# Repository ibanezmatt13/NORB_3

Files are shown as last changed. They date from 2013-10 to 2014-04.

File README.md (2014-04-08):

WARNING - There is a slight design issue with the schematic for the PCB which I had to bodge to get the micro SD working. The VSS pins of the connector should be connected to a GND point on the board, which for some reason it isn't. So, I had to solder a wire going from the connector to a ground point on the board; not pretty but it works.

There are two scripts here, one for delay-driven RTTY, and one for interrupt-driven RTTY. The delay-driven code has been flown and proved to work perfectly; the interrupt-driven code works fine on the ground but has not had an approval flight just yet.

NORB 3
======
NORB 3 is the third generation in the NORB AVR-based HAB tracking PCB series. 

Main Components:
================

NTX2 434MHz Radio Transmitter

Ublox MAX 7 GPS Module

Amtel ATMEGA328P-AU Microcontroller

SHT11 Temperature/Humidity Sensor

TMP102 I2C Temperature Sensor

Micro SD socket

TPS61201 Step-up Boost Regulator

Taoglas GPS Antenna

Info
====

More information including the development, current status and pictures of the tracker can be found at NORB's website:

                                                  http://www.norb.co.uk

What NORB does...
=================

The current software that runs the NORB board does several things:

1.  It uses a special routine to search repeatedly for certain characters over a serial connection to the Ublox GPS         module. Once it picks up the correct beginning of what could be a valid NMEA sentence, it checks for the letter G to     to see if it is the correct sentence. If it is, it passes the sentence as a string to a parse_NMEA function.

2.  The parse_NMEA function is designed to carefully assess whether the sentence contains any anomalies in certain          fields. This could be a lost character during transfer or the sentence may not actually reflect a full GPS lock.        Should this be the case, the parsing is discontinued and the search for another sentence restarts. If it does get       through however, a few tasks are performed...

3.  The time is checked to assess what format it is in and to assess if it is a valid time value. Then the                  Latitude/longitude is converted into decimal degrees for uploading to the spacenear.us server after decoding. 

4.  After the sentence has been stripped down and individual fields of data have been analysed, the program will request     information from the SHT11 temperature and humidity sensor where upon it will parse the data into a suitable format.     The voltage across the battery is also analysed by scaling the analogue value on the correct analogue pin to a value     within the range 0v to 3.3v.

5.  Next, two strings are constructed: a log_datastring and a send_datastring. The log_datastring contains absolutely       all data including voltage and humidity, which will be logged to the SD card. The send_datastring contains only the     bare minimum of required data for basic telemetry, but I couldn't resist adding temperature in there too. I have        done this to further reduce the probability of a decoding error on the ground. ie, more data coming down = more         chance of a bad sentence.

6.  Then, we log the log_datastring to the SD card, and send the send_datastring down over the radio link by splitting      it up into binary digits to toggle the transmit pin on our transmitter. And there you have it! :D

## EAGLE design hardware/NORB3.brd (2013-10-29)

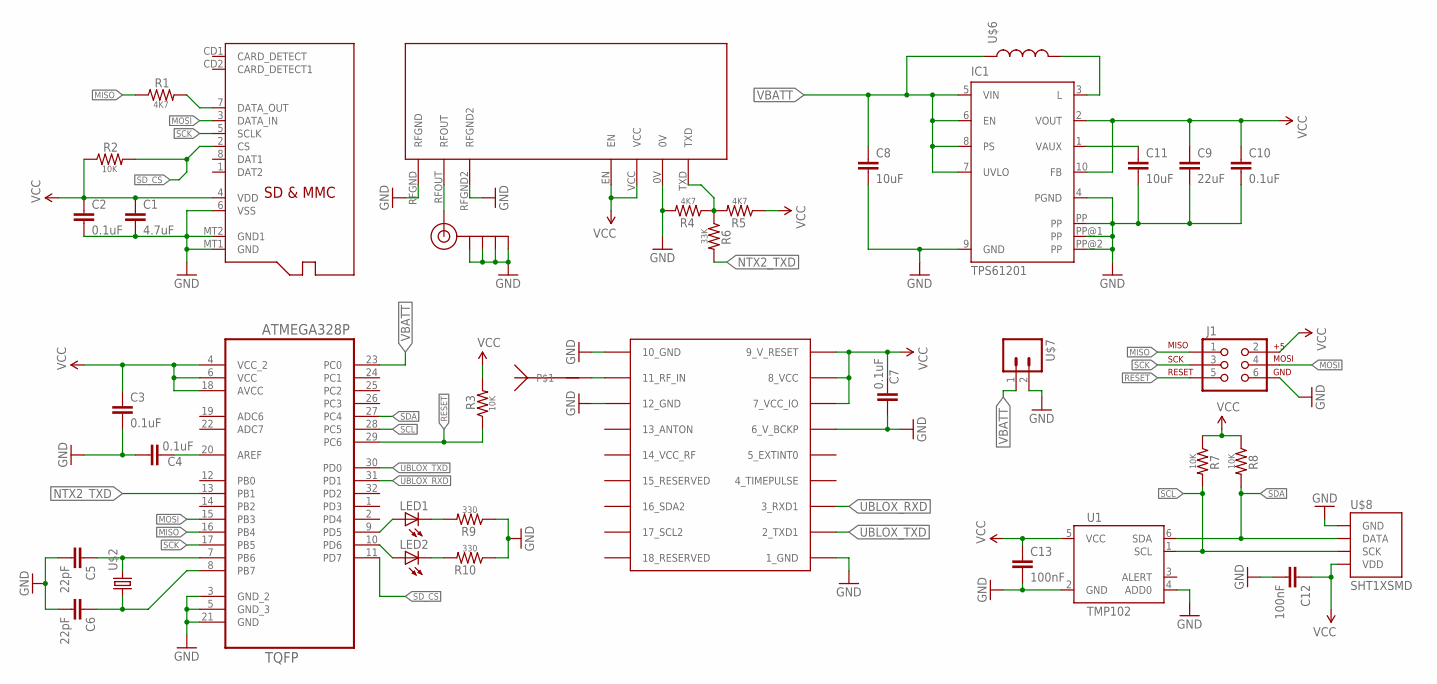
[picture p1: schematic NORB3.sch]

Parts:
C1: 4.7uF; 0603-CAP
C2, C3, C4, C7, C10: 0.1uF; 0603-CAP
C5, C6: 22pF; 0603-CAP
C8: 10uF; 1206
C9: 22uF; 1206
C11: 10uF; 0603-CAP
C12, C13: 100nF; 0603-CAP
IC1: TPS61201; S-PDSO-N10
J1: AVR_SPI_PRG_6PTH; 2X3
J$1: SMA_EDGE; SMA-EDGE
LED1, LED2: LEDCHIPLED_0805; CHIPLED_0805
R1, R4, R5: 4K7; 0603-RES
R2, R3, R7, R8: 10K; 0603-RES
R6: 33K; 0603-RES
R9, R10: 330; 0603-RES
U1: TMP102; SOT563
U2: ATMEGA328P-AU; QFP80P900X900X120-32N
U$1: MICROSD
U$2: ABRACON_ABM3_CRYSTALABM03_HC49; ABM03_HC49
U$3: UBLOX_MAX-6
U$4: TAOGLAS.GP.1575.18.2.A.02
U$5: NTX2
U$6: 2.2uH; ELLVGG_INDUCTOR
U$7: M02-NOSILK
U$8: SHT1XSMD; SHT1X

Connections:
GND: C3.2, C4.2, C5.2, C6.2, C7.2, C8.2, C9.2, C10.2, C11.2, C12.2, C13.2, IC1.4 (PGND), IC1.9 (GND), IC1.PP, IC1.PP@1 (PP), IC1.PP@2 (PP), J1.6, J$1.GND@0 (GND), J$1.GND@1 (GND), J$1.GND@2 (GND), J$1.GND@3 (GND), R4.2, R9.1, R10.1, U1.2 (GND), U1.4 (ADD0), U2.3 (GND_2), U2.5 (GND_3), U2.21 (GND), U$3.1_GND, U$3.6_V_BCKP, U$3.10_GND, U$3.12_GND, U$5.0V, U$5.RFGND, U$5.RFGND2, U$7.2, U$8.1 (GND)
MISO: J1.1, R1.1, U2.16 (PB4)
MOSI: J1.4, U2.15 (PB3), U$1.3 (DATA_IN)
unnamed: R1.2, U$1.7 (DATA_OUT)
unnamed: C5.1, U2.7 (PB6), U$2.2
unnamed: C4.1, U2.20 (AREF)
unnamed: C6.1, U2.8 (PB7), U$2.1
unnamed: U$3.11_RF_IN, U$4.P$1
unnamed: J$1.SIG (SIGNAL), U$5.RFOUT
unnamed: IC1.3 (L), U$6.P$2 (2)
unnamed: R4.1, R5.2, R6.1, U$5.TXD
unnamed: LED1.A, U2.9 (PD5)
unnamed: C11.1, IC1.1 (VAUX)
unnamed: LED1.C, R9.2
unnamed: LED2.A, U2.10 (PD6)
unnamed: LED2.C, R10.2
NTX2_TXD: R6.2, U2.13 (PB1)
RESET: J1.5, R3.1, U2.29 (PC6)
SCK: J1.3, U2.17 (PB5), U$1.5 (SCLK)
SCL: R7.2, U1.1 (SCL), U2.28 (PC5), U$8.3 (SCK)
SDA: R8.2, U1.6 (SDA), U2.27 (PC4), U$8.2 (DATA)
SD_CS: R2.2, U2.11 (PD7), U$1.2 (CS)
UBLOX_RXD: U2.31 (PD1), U$3.3_RXD1
UBLOX_TXD: U2.30 (PD0), U$3.2_TXD1
VBATT: C8.1, IC1.5 (VIN), IC1.6 (EN), IC1.7 (UVLO), IC1.8 (PS), U2.23 (PC0), U$6.P$1 (1), U$7.1
VCC: C1.1, C2.1, C3.1, C7.1, C9.1, C10.1, C12.1, C13.1, IC1.2 (VOUT), IC1.10 (FB), J1.2, R2.1, R3.2, R5.1, R7.1, R8.1, U1.5 (VCC), U2.4 (VCC_2), U2.6 (VCC), U2.18 (AVCC), U$1.4 (VDD), U$3.7_VCC_IO, U$3.8_VCC, U$3.9_V_RESET, U$5.EN, U$5.VCC, U$8.4 (VDD)
VSS: C1.2, C2.2, U$1.6 (VSS), U$1.MT1 (GND), U$1.MT2 (GND1)

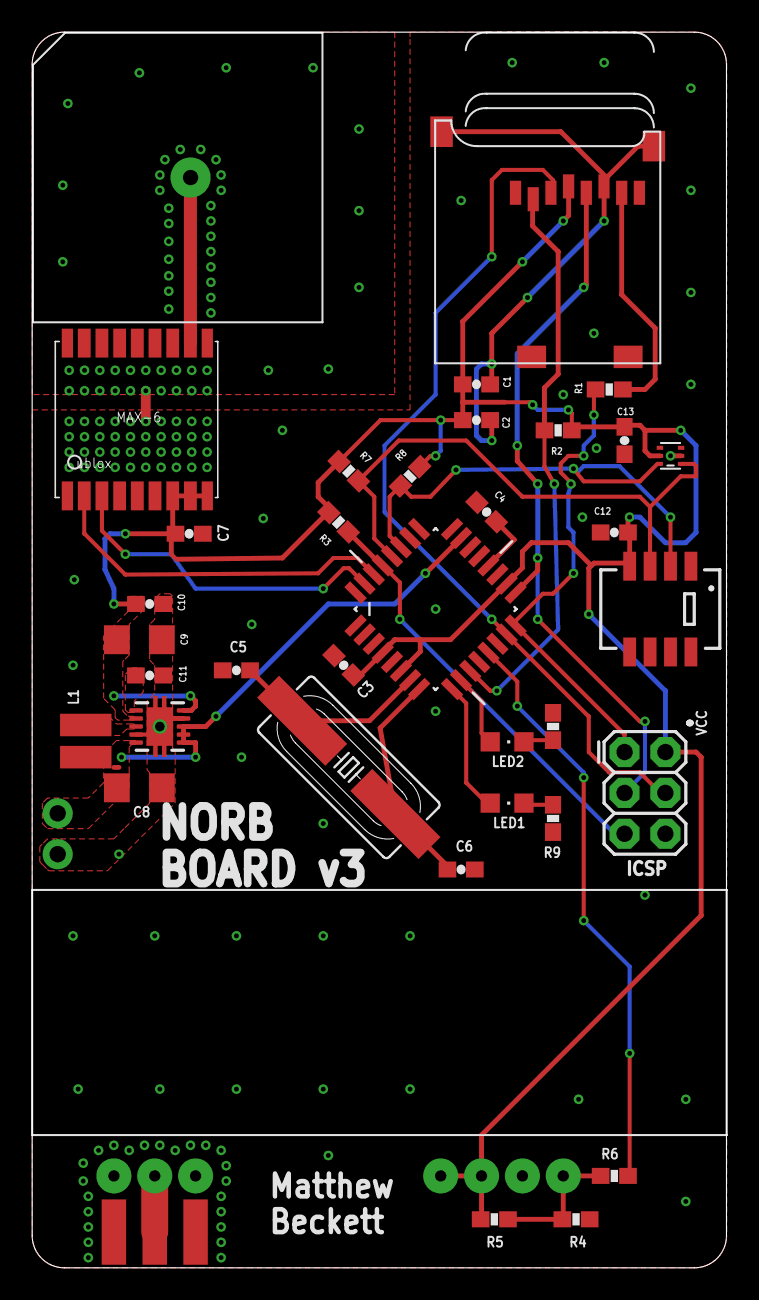
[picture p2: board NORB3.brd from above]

Board: 2 copper layers, 43.2 x 76.8 mm, 38 parts (0 on the bottom side), 27 nets.

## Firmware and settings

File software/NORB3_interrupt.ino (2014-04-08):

#include <util/crc16.h>
#include <SHT1x.h>
#include <SD.h>

#define RADIOPIN 9
#define LED_1 5
#define LED_2 6  
#define dataPin A4     
#define clockPin A5
#define BAUD_RATE 300 // change this value to desired baud rate

SHT1x sht1x(dataPin, clockPin); 
File logfile; // file object for SD

int counter = 0; // sentence id
int tx_status = 0;
char *ptr = NULL;
char currentbyte;
int currentbitcount;

volatile boolean sentence_needed;

char send_datastring[102] = "";

// this command will set flight mode
uint8_t setNav[] = {
    0xB5, 0x62, 0x06, 0x24, 0x24, 0x00, 0xFF, 0xFF, 0x06, 0x03, 0x00, 0x00, 0x00, 0x00, 0x10, 0x27, 0x00, 0x00, 
    0x05, 0x00, 0xFA, 0x00, 0xFA, 0x00, 0x64, 0x00, 0x2C, 0x01, 0x00, 0x00, 0x00, 0x00, 0x00, 0x00, 0x00, 0x00, 
    0x00, 0x00, 0x00, 0x00, 0x00, 0x00, 0x16, 0xDC };



ISR(TIMER1_COMPA_vect){
	
  
  
  switch (tx_status){
    
    case 0: // when the next byte needs to be gotten
      if (ptr){ // if the pointer is valid
	currentbyte = *ptr;
        if (currentbyte){ // if there exists a byte at the pointer
          tx_status = 1;
          sentence_needed = false;
          digitalWrite(LED_1, LOW);
        }
        else {
          sentence_needed = true;
          digitalWrite(LED_1, HIGH);
          break;
        }
      }
      else {
        sentence_needed = true;
        digitalWrite(LED_1, HIGH);
        break;
      }
    
    case 1: // first bit about to be sent
      rtty_txbit(0); // send start bit
      tx_status = 2;
      currentbitcount = 1; // set bit count to 0 ready for incrementing to 7 for last bit of a ASCII-7 byte
      break;
			
    case 2: // normal status, transmitting bits of byte (including first and last)
      if (currentbyte & 1){
        rtty_txbit(1);
      }
      else {
	rtty_txbit(0);
      }
			
      if (currentbitcount == 7){ // if we've just transmitted the final bit of the byte
        tx_status = 3;
      }
      
      currentbyte = currentbyte >> 1; // shift all bits in byte 1 to right so next bit is LSB
      currentbitcount++;
      break;
			
    case 3: // if all bits have been transmitted and we need to send the first of two stop bits
      rtty_txbit(1); // send first stop bit
      tx_status = 4;
      break;
			
    case 4: // ready to send the last of two stop bits
      rtty_txbit(1); // send the final stop bit
      ptr++; // increment the pointer for reading next byte in buffer
      tx_status = 0;
      break;
      
    }

}


 
void rtty_txbit (int bit)
{
  digitalWrite(RADIOPIN, bit);
  //digitalWrite(LED_2, bit);
  //digitalWrite(LED_1, bit);                      
}  

 
// function to convert latitude into decimal degrees
int check_latitude(char* latitude, char* ind, float* new_latitude)
{
  float result = 0;
 
  if (strlen(ind)==1)
  {
    result+=(latitude[0]-'0')*10;
    result+=(latitude[1]-'0');
    result+=(strtod(&latitude[2],NULL) /60);
        
  if (strcmp(ind,"S")==0)
  {
    result*=-1;
  }
        
  *new_latitude = result;
  return 1;
  }
  else
  {
    return -1;
  }
}
 

char *ltrim(char *string) { return(*string == ' ' ? string + 1 : string); }


//function to calculate and store temp/humdity in given location in memory
void SHT11(float* temp, float* hum)
{
  float temp_c;
  float humidity;
  
  temp_c = sht1x.readTemperatureC();
  humidity = sht1x.readHumidity();
  
  *temp = temp_c;
  *hum = humidity;
}
 
 
// function to convert longitude into decimal degrees
int check_longitude(char* longitude, char* ind, float* new_longitude)
{
  float result = 0;
  
  if (strlen(ind)==1)
  {
    result+=(longitude[0]-'0')*100;
    result+=(longitude[1]-'0')*10;
    result+=(longitude[2]-'0');
    result+=(strtod(&longitude[3],NULL) /60);

  if (strcmp(ind,"W")==0)
  {
    result*=-1;
  }
        
  *new_longitude = result;
  return 1;
  }
  else
  {
    return -1;
  }
}
 
 
 
// function to parse NMEA data and send to NTX2
int parse_NMEA(char* mystring, int flightmode)
{
  float new_latitude;
  float new_longitude;
  char new_lat[12];
  char new_lon[12];
  char* trimmed_lon;
  char time[12];
  int time_length;
  char identifier[7];
  char latitude[12];
  char north_south[2];
  char longitude[12];
  char east_west[2];
  int lock;
  int satellites;
  char altitude[10];
  int check_latitude_error;
  int check_longitude_error;
  char* callsign = "$$$$NORB2";
  float vbatt;
  char voltage[10];
  float temp;
  float hum;
  char temp_string[10];
  char hum_string[10];
  char log_datastring[102] = "";
  
  
 
  // split NMEA string into individual data fields and check that a certain number of values have been obtained
  // $GPGGA,212748.000,5056.6505,N,00124.3531,W,2,07,1.8,102.1,M,47.6,M,0.8,0000*6B
  if (sscanf(mystring, "%6[^,],%11[^,],%11[^,],%1[^,],%11[^,],%1[^,],%d,%d,%*[^,],%9[^,]", identifier, time, latitude, north_south, longitude, east_west, &lock, &satellites, altitude) == 9)
  {
    // check for the identifer being invalid
    if (strncmp(identifier, "$GPGGA", 6) != 0)
    {
      return 0;
    }
    
    // check for a valid lock
    if (lock == 0)
    {
      digitalWrite(LED_2, HIGH);
      return 0;
    }
    
    time_length = strlen(time); //get length of time
  
    // check time is in the format: HHMMSS unless either already set or NMEA input was invalid
    if (time_length > 6)
    {
      sscanf(time, "%[^.]", time);
    }
    else if (time_length < 6)
    {  
      return 0;
    }
    
    // store the return value of the latitude/longitude functions accordingly
    check_latitude_error = check_latitude(latitude, north_south, &new_latitude);
    check_longitude_error = check_longitude(longitude, east_west, &new_longitude);
   
    
    // if check_latitude() failed
    if (check_latitude_error == -1)
    {
      return 0;
    }
    
    // if check_longitude() failed
    if (check_longitude_error == -1)
    {
      return 0;
    }
    
    
    vbatt = ((3.3 / 1024)* analogRead(0));
    SHT11(&temp, &hum);
    
    // convert floats to strings
    dtostrf(new_latitude,9,6,new_lat);
    dtostrf(new_longitude,9,6,new_lon);
    dtostrf(vbatt,3,2,voltage);
    dtostrf(temp,3,2,temp_string);
    dtostrf(hum,3,2,hum_string);
    
    trimmed_lon = ltrim(new_lon);
    
    while (!sentence_needed){
      // wait until sentence needed
    }
    sprintf(send_datastring, "%s,%d,%s,%s,%s,%s,%d,%d,%d,%s", callsign, counter ,time, new_lat, new_lon, altitude, lock, flightmode, satellites, temp_string); 
    digitalWrite(LED_2, LOW);
    unsigned int CHECKSUM = gps_CRC16_checksum(send_datastring);  // Calculates the checksum for this datastring
    char checksum_str[7];
    sprintf(checksum_str, "*%04X\n", CHECKSUM);
    strcat(send_datastring,checksum_str);
    counter++;
    ptr = send_datastring;
    
    sprintf(log_datastring, "%s,%d,%s,%s,%s,%s,%d,%d,%d,%s,%s,%s", callsign, counter ,time, new_lat, new_lon, altitude, lock, flightmode, satellites, voltage, temp_string, hum_string);
    
    logfile = SD.open("data.txt", FILE_WRITE); // open logfile
    
    if (logfile){  // if log file opened ok
      logfile.println(log_datastring); //write datastring to file
      logfile.close();
    } else {
      logfile.close();
    }
    
  }
  else
  {
    digitalWrite(LED_2, HIGH);
    return 0;
  }
}


void initialise_interrupt() 
{
  // initialize Timer1
  cli();          // disable global interrupts
  TCCR1A = 0;     // set entire TCCR1A register to 0
  TCCR1B = 0;     // same for TCCR1B
  OCR1A = F_CPU / 1024 / (BAUD_RATE - 1);  // set compare match register to desired timer count
  TCCR1B |= (1 << WGM12);   // turn on CTC mode:
  // Set CS10 and CS12 bits for:
  TCCR1B |= (1 << CS10);
  TCCR1B |= (1 << CS12);
  // enable timer compare interrupt:
  TIMSK1 |= (1 << OCIE1A);
  sei();          // enable global interrupts
}

 
void setupGPS()
{
  //disable unwanted NMEA sentences
  Serial.println("$PUBX,40,GLL,0,0,0,0*5C");
  delay(1000);
  Serial.println("$PUBX,40,GSA,0,0,0,0*4E");
  delay(1000);
  Serial.println("$PUBX,40,RMC,0,0,0,0*47");
  delay(1000);
  Serial.println("$PUBX,40,GSV,0,0,0,0*59");
  delay(1000);
  Serial.println("$PUBX,40,VTG,0,0,0,0*5E");
  delay(1000);
}
 
// Send a byte array of UBX protocol to the GPS
void sendUBX(uint8_t *MSG, uint8_t len) {
  for(int i=0; i<len; i++) {
    Serial.write(MSG[i]);
  }
  Serial.println();
}

uint16_t gps_CRC16_checksum (char *string)
{
  size_t i;
  uint16_t crc;
  uint8_t c;
 
  crc = 0xFFFF;
 
  // Calculate checksum ignoring the first two $s
  for (i = 4; i < strlen(string); i++)
  {
    c = string[i];
    crc = _crc_xmodem_update (crc, c);
  }
 
  return crc;
}    

int getUBX_ACK(uint8_t *MSG) {
  uint8_t b;
  uint8_t ackByteID = 0;
  uint8_t ackPacket[10];
  unsigned long startTime = millis();
 
  // Construct the expected ACK packet    
  ackPacket[0] = 0xB5;        // header
  ackPacket[1] = 0x62;        // header
  ackPacket[2] = 0x05;        // class
  ackPacket[3] = 0x01;        // id
  ackPacket[4] = 0x02;        // length
  ackPacket[5] = 0x00;
  ackPacket[6] = MSG[2];        // ACK class
  ackPacket[7] = MSG[3];        // ACK id
  ackPacket[8] = 0;                // CK_A
  ackPacket[9] = 0;                // CK_B
 
  // Calculate the checksums
  for (uint8_t i=2; i<8; i++) {
    ackPacket[8] = ackPacket[8] + ackPacket[i];
    ackPacket[9] = ackPacket[9] + ackPacket[8];
  }
 
  while (1) {
 
    // Test for success
    if (ackByteID > 9) {
      // All packets in order!
      return 1;
    }
 
    // Timeout if no valid response in 3 seconds
    if (millis() - startTime > 3000) { 
      return 0;
    }
 
    // Make sure data is available to read
    if (Serial.available()) {
      b = Serial.read();
 
      // Check that bytes arrive in sequence as per expected ACK packet
      if (b == ackPacket[ackByteID]) { 
        ackByteID++;
      } 
      else {
        ackByteID = 0;        // Reset and look again, invalid order
      }
 
    }
  }
}
 
void setup()
{
  Serial.begin(9600);
  pinMode(RADIOPIN, OUTPUT);
  pinMode(LED_1, OUTPUT);
  pinMode(LED_2, OUTPUT);
  pinMode(10, OUTPUT); // needed for SD library
  SD.begin(7);
  setupGPS();
  initialise_interrupt();
}
 
void loop()
{
  static char datastring[100];
  char character;
  static int n = 0;
  int flightmode = 0;
 
  if (Serial.available()){
    character = Serial.read();
    
    if (character == '$'){
      n = 0;
      datastring[n] = character;
      n = 1;
    }
    
    else if (character == '\n'){
      datastring[n] = '\0';
      flightmode = 0;
      sendUBX(setNav, sizeof(setNav)/sizeof(uint8_t)); // set flight mode
      flightmode = getUBX_ACK(setNav); // check flight mode enabled
      parse_NMEA(datastring, flightmode);
      n = 0;
      flightmode = 0;
    }
    
    else if (n > 0){
      datastring[n] = character;
      n++;
    }
    
    if (n >= 98){
      n = 0;
    }
  }
}

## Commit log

2014-01-09 Update NORB.bas
    Basic script to take a 2 minute video and save in a loop throughout the flight. This avoids the max recording limit set on modern cameras for tax reasons.
2014-04-03 Create KMLCreator.py
    A quick python sketch to extract the latitude and longitude from a datafile and write to a new file for use in GEarth.
2014-04-07 Added interrupt code
    Note, SD not supported in this version

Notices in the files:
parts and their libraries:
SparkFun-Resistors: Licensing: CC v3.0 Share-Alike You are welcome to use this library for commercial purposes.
